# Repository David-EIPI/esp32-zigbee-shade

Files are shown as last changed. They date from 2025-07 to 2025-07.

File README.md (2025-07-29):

# esp32-zigbee-shade

## Overview

This external window shade is designed to shield the room from sunlight, reducing the load on the air conditioner. I upgraded a basic corded roller shade by integrating a small DC motor and a Zigbee controller compatible with my Home Assistant network.

## Firmware

The firmware is written in C and built using `idf.py`.
It exposes 2 endpoints with 3 clusters:

* **Window covering** (shade control)
* **OTA** (remote firmware upgrade)
* **Temperature measurement** (on-chip temperature sensor)

The temperature sensor reports via Zigbee to monitor the temperature inside the control box, as summer ambient temperatures often exceed 35°C, and the enclosure tightly houses both the ESP32 and the motor driver.

See [here](https://github.com/David-EIPI/esp32-zigbee-light/blob/main/BUILD.md) instructions on building the firmware using `idf.py` on Linux.

## Hardware

### Mechanical

This window cover is based on the VICLLAX 5×6 ft corded roll-up shade, which uses an aluminum tube with a 1 1/8" (28 mm) inner diameter.

Several inexpensive DC motors with pre-assembled gearheads are available online, commonly found as clones of the Bringsmart High Torque Worm Gear DC motor. Most of these motors use gearheads with D-shaped shafts, predominantly 8 mm but occasionally 6 mm.

These motors and gearboxes come in various voltages and torque ratings. I used a 12 V motor equipped with a 200× ratio gearbox rated for 4 kg·cm torque. This choice turned out to be excessive, as a gearbox with a 60× or 80× ratio would have been sufficient.

To couple the motor to the roller tube, I repurposed Zemismart’s replacement 28 mm nylon gears, removing one tooth from each side and filing the D-shaped channel to match the motor shaft.

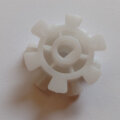
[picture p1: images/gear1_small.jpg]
OriginalGear The original gear

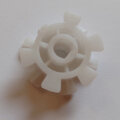
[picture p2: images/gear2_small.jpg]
ModifiedGear Modified gear
\
*The original gear compared to the modified gear (two teeth removed, D-shape filed).*

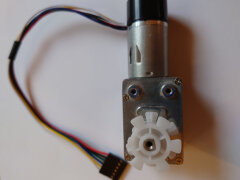
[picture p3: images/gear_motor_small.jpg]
GearMotor Gear fits the motor
\
*Gear mounted on the motor shaft.*

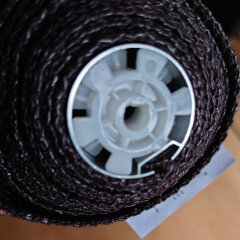
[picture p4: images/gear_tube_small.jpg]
GearTube Gear fits the tube
\
*Gear inserted into the shade tube.*

For motor mounting, I modified the original bracket supplied with the shade. I broke off the support lip, drilled two additional holes, and added a countersunk hole at the existing cut. The modified bracket is shown below:

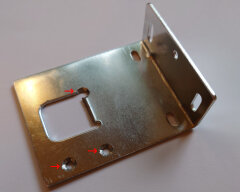
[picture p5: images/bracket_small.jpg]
Bracket


The image below shows the fully assembled motor with the coupling gear:

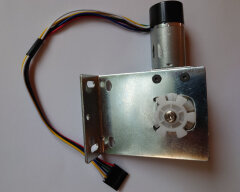
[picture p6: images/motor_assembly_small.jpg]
Assembly


### Electronics

The control system uses an ESP32-H2 chip on Tenstar’s Supermini board (or a clone). [This board sometimes exhibits startup issues](https://github.com/David-EIPI/esp32-zigbee-light) when powered from a standalone DC-DC converter. Although the board already has an RC circuit on its reset line, it is apparently insufficient, as intermittent boot failures occur on power-up. I resolved this issue by soldering an additional 0.22 µF capacitor in parallel with the existing one.

The ESP32-H2 Supermini clones available on Aliexpress vary. The most notable difference is component placement: some boards have all components mounted on the top side, while other (usually cheaper) versions have components on both sides. For the double-sided boards, the additional capacitor should be soldered on the bottom side, as shown in the photo. Although I only had 0603-sized capacitors at hand, it fit comfortably next to the existing one.

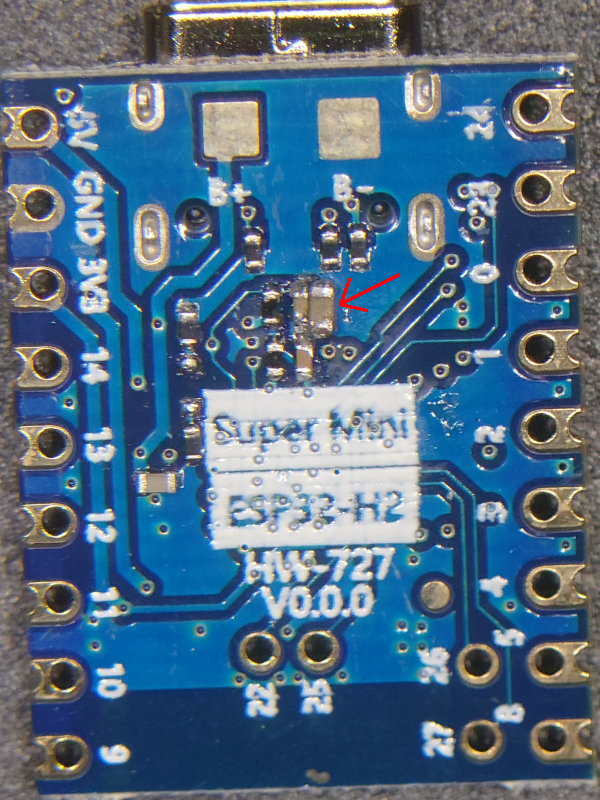
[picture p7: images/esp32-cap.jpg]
Bottom side cap Capacitor


Due to bottom-side components, the ESP32-H2 board must be mounted above the mainboard:

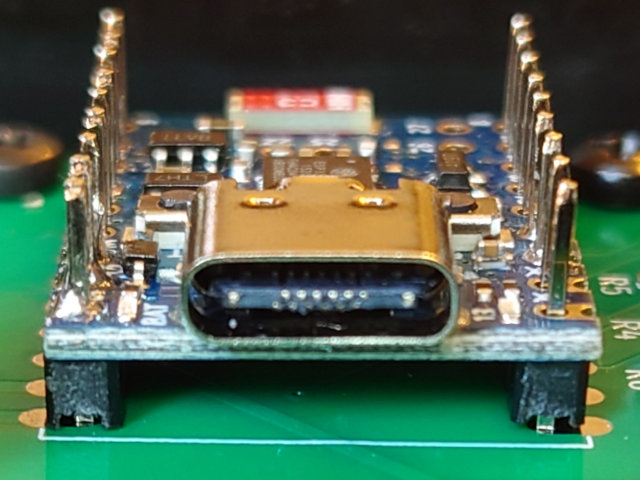
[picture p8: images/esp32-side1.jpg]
Elevated board Elevated


The motor driver uses a DRV8871 chip from Texas Instruments. It accepts a PWM control signal, easily generated using the standard ESP32 `ledc` controller.

The motor features a rotary encoder interfaced to the ESP32’s standard pulse-counter controller. This encoder maintains consistent upper and lower travel limits and allows precise partially-open positioning of the shade.

A notable drawback of this motor is its hardwired, non-weatherproof cable. Its durability in summer humidity remains uncertain, and some corrosion is likely inevitable. To minimize electrochemical corrosion, I designed the control circuit to disconnect power from the motor and encoder when the shade is stationary.

The final assembly fits neatly into the Serpac 110i BK enclosure. I only needed to cut openings for the 6-pin motor connector (on the left) and the power jack (on the right):

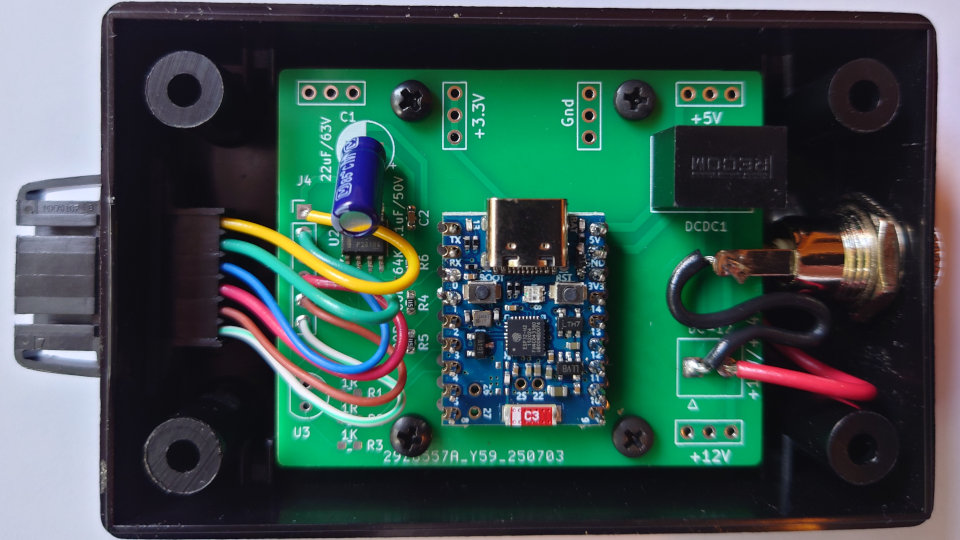
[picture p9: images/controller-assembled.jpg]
Controller assembly Controller


Since the motor connector is not polarized it may be a good idea to mark the connector orientation on the enclosure side.

## ZHA quirk

Although ZHA supports window coverings, additional configuration using a quirk is required. The quirk provides coverage percentage display, lift velocity settings, and essential calibration buttons for setting upper and lower limits.

The screenshot below shows the device page (quirk applied):

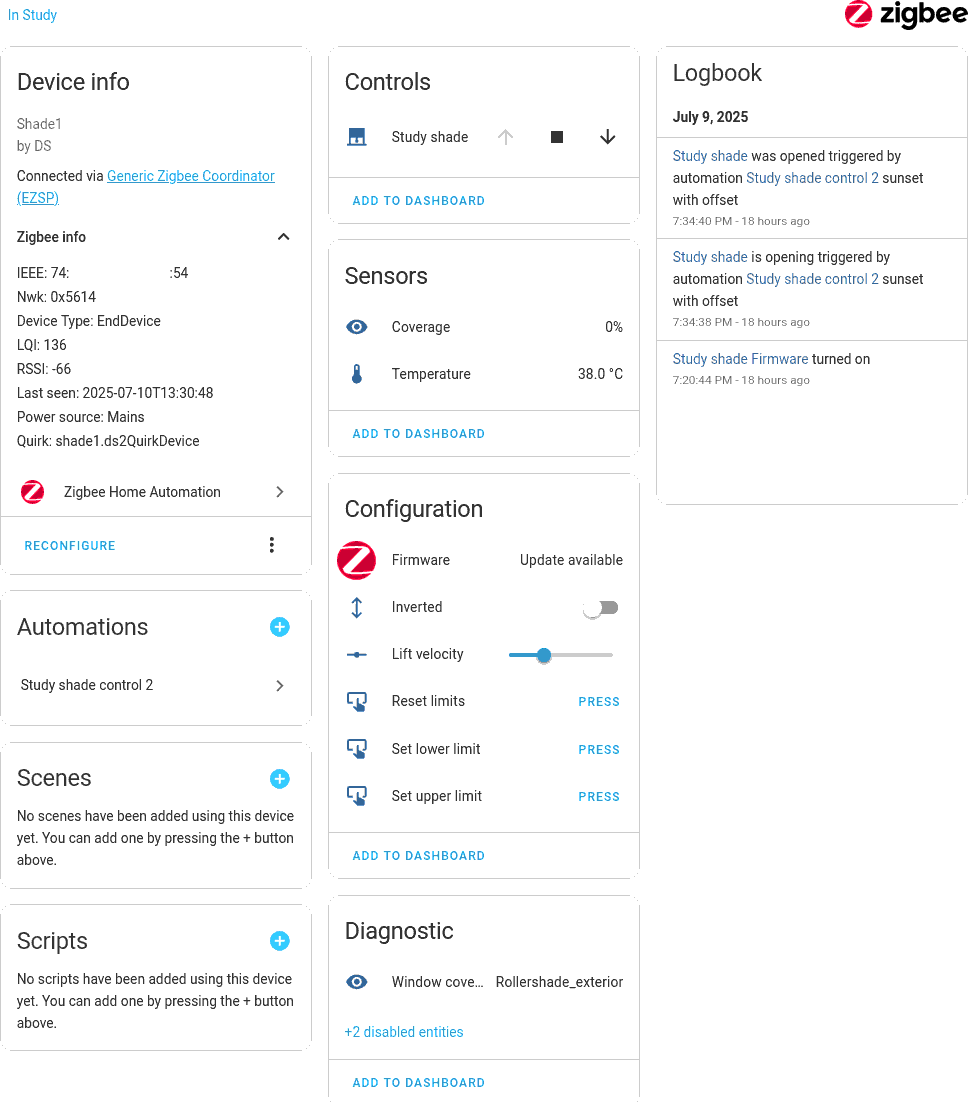
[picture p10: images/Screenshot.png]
Device info


Calibration of limits must be completed before using the shade for the first time. The calibration procedure is as follows:

* Press "↓" to start lowering the shade, stopping roughly halfway.
  This step isn't strictly required, but it reduces the likelihood of pulse counter overflow, as the pulse counter range is limited to 16 bits.
* Press "reset limits".
* Press "↑" to raise the shade, stopping at the desired upper position. Then press "Set upper limit" to record this position.
* Press "↓" again, stopping at the desired lower position. Then press "Set lower limit" to record this position.

Depending on Zigbee network topology, commands may take about a second to process. Thus, if the motor rolls quickly, reducing the lift velocity before calibration may improve accuracy.

## Over-the-air (OTA) upgrade

The firmware supports OTA upgrades. ESP's Zigbee library handles most tasks, leaving only four essential `esp_ota_*` function calls (`begin`, `data`, `write`, and `end`) for firmware implementation, aside from cluster allocation and error checking. The SDK provides an image builder tool (`image_builder_tool.py`) to convert compiled firmware into OTA format (see the `ota_image.sh` script for a usage example).

On the Home Assistant side, the Zigpy configuration should be added to `configuration.yaml` under the `zha:` section, as illustrated below:

```
zha:
  zigpy_config:
    ota:
      extra_providers:
        - type: zigpy_local
          index_file: /config/zha_ota/local_index.json
        - type: advanced
          warning: I understand I can *destroy* my devices by enabling OTA
              updates from files. Some OTA updates can be mistakenly applied to the
              wrong device, breaking it. I am consciously using this at my own risk.
          path: /config/zha_ota
```

OTA update files (JSON and BIN) should be uploaded to the specified directory (`/config/zha_ota` in this example). When using the JSON OTA provider, Home Assistant will display firmware version and release notes from the provided JSON file.

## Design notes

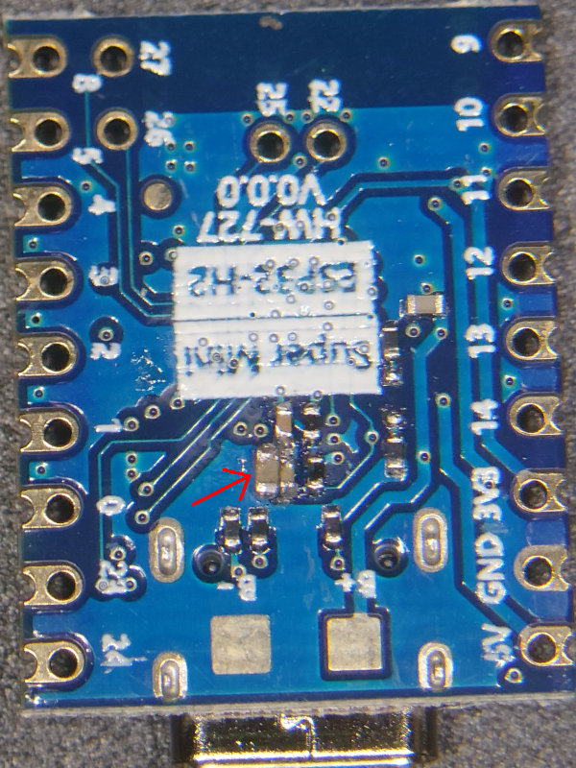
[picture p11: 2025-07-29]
images/esp32-cap1.jpg

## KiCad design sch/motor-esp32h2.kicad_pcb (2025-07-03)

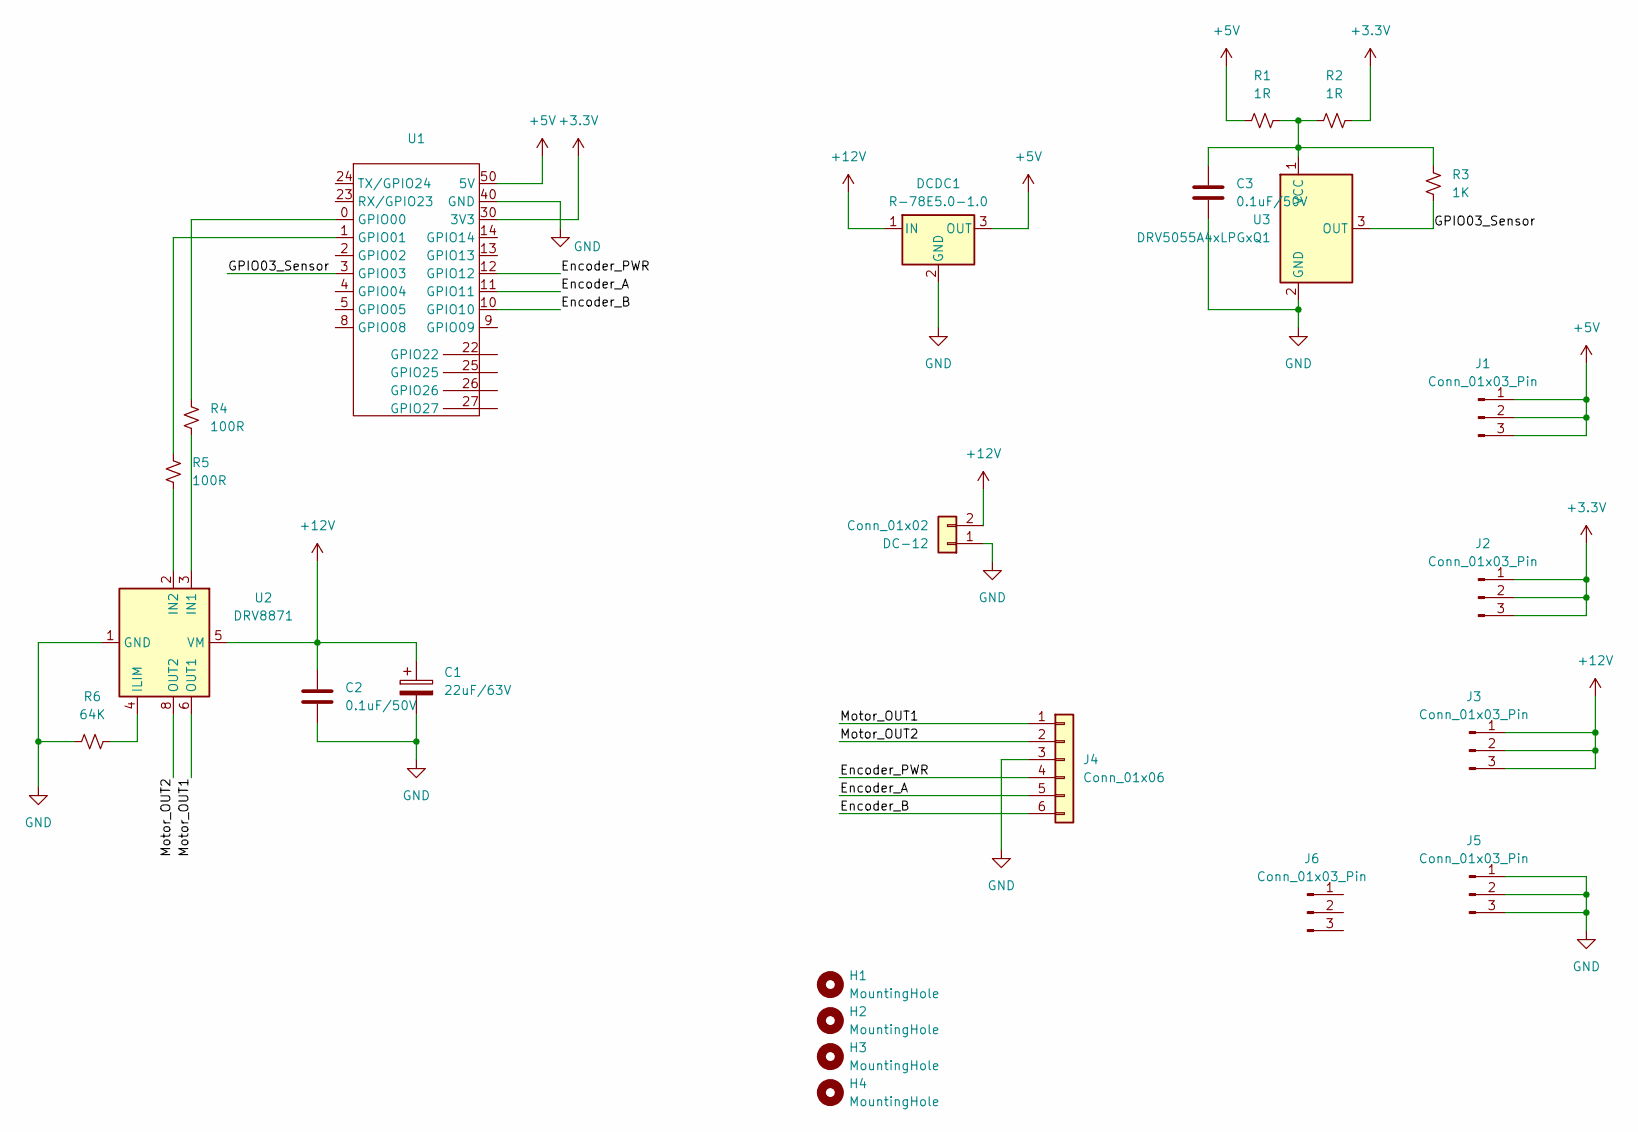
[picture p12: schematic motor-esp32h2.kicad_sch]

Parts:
C1: 22uF/63V; CP_Radial_D6.3mm_P2.50mm
C2, C3: 0.1uF/50V; C_0603_1608Metric_Pad1.08x0.95mm_HandSolder
DC-12: Conn_01x02; TE_826576-2_1x02_P3.96mm_Vertical
DCDC1: R-78E5.0-1.0; Converter_DCDC_RECOM_R-78E-0.5_THT
H1, H2, H3, H4: MountingHole; MountingHole_2.7mm_M2.5
J1, J2, J3, J5, J6: Conn_01x03_Pin; PinHeader_1x03_P2.54mm_Vertical
J4: Conn_01x06; PinHeader_1x06_P2.54mm_Vertical
R1, R2: 1R; R_0603_1608Metric_Pad0.98x0.95mm_HandSolder
R3: 1K; R_0603_1608Metric_Pad0.98x0.95mm_HandSolder
R4, R5: 100R; R_0603_1608Metric_Pad0.98x0.95mm_HandSolder
R6: 64K; R_0603_1608Metric_Pad0.98x0.95mm_HandSolder
U1: ESP32-H2-SuperMini
U2: DRV8871; Texas_HTSOP-8-1EP_3.9x4.9mm_P1.27mm_EP2.95x4.9mm_Mask2.4x3.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
U3: DRV5055A4xLPGxQ1; TO-92_Inline

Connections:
+3.3V: J2.1, J2.2, J2.3, R2.2, U1.30 (3V3)
+5V: DCDC1.3 (OUT), J1.1, J1.2, J1.3, R1.1, U1.50 (5V)
+12V: C1.1, C2.1, DC-12.2, DCDC1.1 (IN), J3.1, J3.2, J3.3, U2.5 (VM)
/Encoder_A: J4.5, U1.11 (GPIO11)
/Encoder_B: J4.6, U1.10 (GPIO10)
/Encoder_PWR: J4.4, U1.12 (GPIO12)
/GPIO03_Sensor: R3.1, U1.3 (GPIO03), U3.3 (OUT)
/Motor_OUT1: J4.1, U2.6 (OUT1)
/Motor_OUT2: J4.2, U2.8 (OUT2)
GND: C1.2, C2.2, C3.2, DC-12.1, DCDC1.2 (GND), J4.3, J5.1, J5.2, J5.3, R6.1, U1.40 (GND), U2.1 (GND), U2.7 (GND), U2.9 (GND), U3.2 (GND)
unnamed: R4.1, U1.0 (GPIO00)
unnamed: R5.1, U1.1 (GPIO01)
unnamed: R6.2, U2.4 (ILIM)
unnamed: R4.2, U2.3 (IN1)
unnamed: R5.2, U2.2 (IN2)
unnamed: C3.1, R1.2, R2.1, R3.2, U3.1 (VCC)

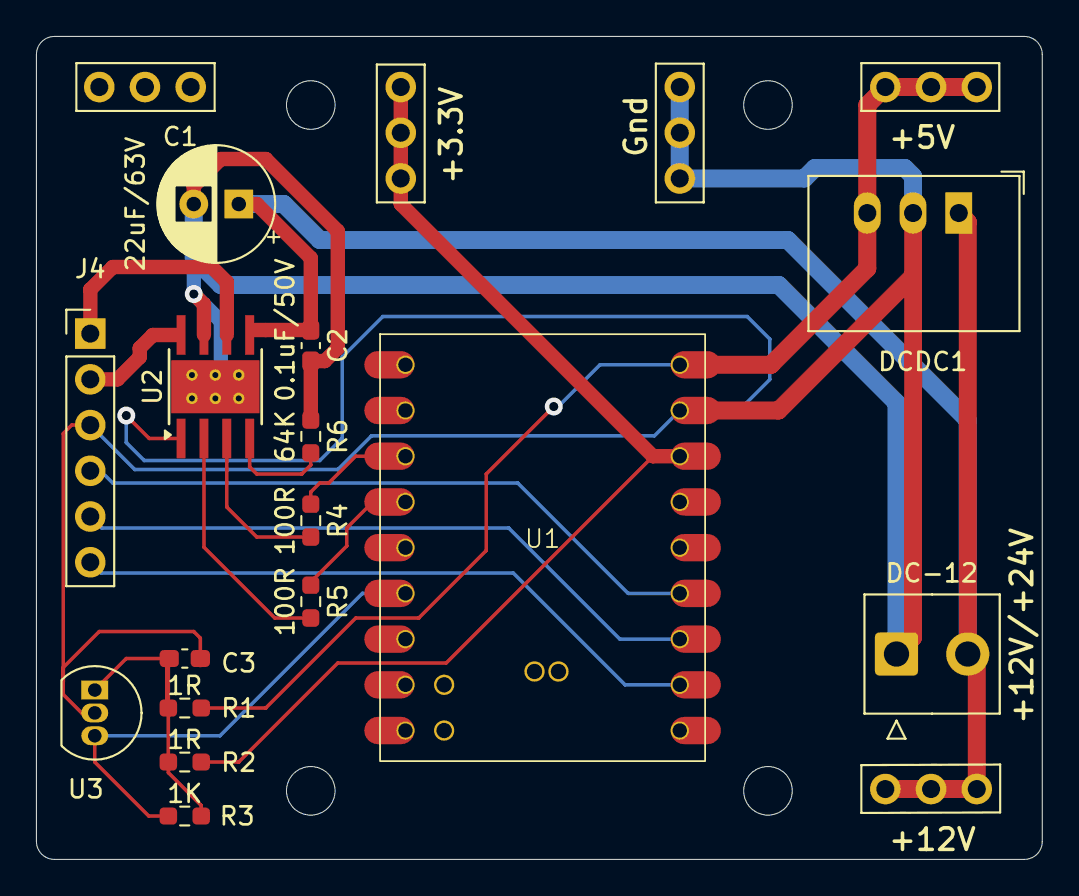
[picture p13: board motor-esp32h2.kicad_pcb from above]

Board: 2 copper layers, 55.9 x 45.7 mm, 24 parts (0 on the bottom side), 16 nets.

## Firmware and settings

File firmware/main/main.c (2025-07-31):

/*
 * Zigbee Roller Shade Example
 *
 * Unless required by applicable law or agreed to in writing, this
 * software is distributed on an "AS IS" BASIS, WITHOUT WARRANTIES OR
 * CONDITIONS OF ANY KIND, either express or implied.
 * 2025/07
 * License: BSD-2
 */

#include <string.h>
#include "freertos/FreeRTOS.h"
#include "freertos/task.h"
#include "esp_check.h"
#include "esp_zigbee_core.h"
#include "esp_log.h"
#include "nvs_flash.h"
#include "ha/esp_zigbee_ha_standard.h"
#include "driver/gpio.h"
#include "driver/temperature_sensor.h"
#include "main.h"
#include "clock.h"
#include "encoder.h"
#include "motor.h"
#include "ota.h"


#if !defined ZB_ED_ROLE
#error Define ZB_ED_ROLE in idf.py menuconfig to compile light (End Device) source code.
#endif


enum _queue_message_code {
    QM_UNKNOWN = 0,
    QM_FROM_ENCODER,
    QM_ZIGBEE_STOP,
    QM_ZIGBEE_UP,
    QM_ZIGBEE_DOWN,
    QM_ZIGBEE_TO_VALUE,
    QM_ZIGBEE_TO_PERCENTAGE,
    QM_ZIGBEE_SET_UPPER,
    QM_ZIGBEE_SET_LOWER,
    QM_ZIGBEE_RESET_LIMITS,
    QM_ZIGBEE_SET_VELOCITY,
    QM_ZIGBEE_SET_MODE,
};


static const char *ZB_TAG = "APP_ZIGBEE";
static const char *MAIN_TAG = "APP_MAIN";

static const unsigned indication_led_pin = 13;

static const uint32_t timer_resolution = 10 * 1000;
static gptimer_handle_t timer = 0;

TaskHandle_t motorTaskHandle = NULL;

static temperature_sensor_handle_t temp_handle = NULL;
static float temperature_sensor_value = 0;


/* The queue is to be created to hold a maximum of 16 uint32_t  variables. */
#define QUEUE_LENGTH      16
#define QUEUE_ITEM_SIZE   sizeof( uint32_t )

/* The variable used to hold the queue's data structure. */
static StaticQueue_t xStaticQueue;

/* The array to use as the queue's storage area. This must be at least uxQueueLength * uxItemSize bytes. */
static uint8_t ucQueueStorageArea[ QUEUE_LENGTH * QUEUE_ITEM_SIZE ];

/* Main task queue is used to send commands and data to the main task */
QueueHandle_t xMainQueue;

/* Position monitoring. current_pos = last reading from the encoder */
static int32_t currentPosition = 0;
/* Position monitoring. previous_pos = previous reading */
static int previousPosition = 0;
/* Position monitoring. target_pos = requested position.
The motor must spin towards target_pos, otherwise we should stop it. */
static int targetPosition = 0;

/*
    Save position to NVS when it changes by this amount.
    Position is also saved every time the motor stops.
 */
static const int32_t movingSaveDelta = ENCODER_PULSE_PER_REV;
/*
    NVS saving delta when motor is stationary accounts for backlash.
*/
static const int32_t staticSaveDelta = 20;

/* Approximate lift velocity at max motor speed, cm/s */
static const int maxLiftVelocity = 10;

/* Lift velocity requested via Zigbee */
static int32_t zbLiftVelocity = 5;

/* Upper and lower lift limits. Must be calibrated via Zigbee */
static int32_t upperLiftLimit = ENCODER_MAX_LIMIT;
static int32_t lowerLiftLimit = ENCODER_MIN_LIMIT;

/* Fixed upper and lower limits reported to clients */
static int32_t zb_UpperLiftLimit = 180;
static int32_t zb_LowerLiftLimit = 0;

/* User configured coverage limit, % */
static int32_t zb_userPercentageLimit = 100;

/* Inversion flag. Changes percentage assigment and up/down buttons' directions. */
static int zb_Inversion = 0;

/* NVS keys */
const char ZB_STORAGE_NAMESPACE[] = "zb_storage";

static char nvs_UpperLimit[] = "W_UL";
static char nvs_LowerLimit[] = "W_LL";
static char nvs_zbUpperLimit[] = "WZUL";
static char nvs_zbLowerLimit[] = "WZLL";
static char nvs_Velocity[] = "W_Ve";
static char nvs_ModeAttr[] = "W_MA";
static char nvs_CurrentPosition[] = "W_CP";

/********************* Utility functions **************************/

static int encoder_to_zigbee(int position, int zb_min, int zb_max)
{
    if (zb_min == zb_max ||
        upperLiftLimit == lowerLiftLimit) {
        return 0;
    }

    int encmin = lowerLiftLimit;
    int diff = upperLiftLimit - lowerLiftLimit;

/* Allow inversion */
    if (diff < 0) {
        diff = -diff;
        encmin = upperLiftLimit;
    }

    int zb_pos = zb_min + ((position - encmin) * (zb_max - zb_min)) / diff;
    if (zb_pos < zb_min) zb_pos = zb_min;
    else if (zb_pos > zb_max) zb_pos = zb_max;
    return zb_pos;
}

static int encoder_to_zigbee_units(int position)
{
    return encoder_to_zigbee(position, zb_LowerLiftLimit, zb_UpperLiftLimit);
}

static int encoder_to_zigbee_percentage(int position)
{
    uint8_t p = encoder_to_zigbee(position, 0, 100);
    if (!zb_Inversion)
        p = 100 - p;

    return p;
}

static int zigbee_to_encoder(int zb_position, int zb_min, int zb_max)
{
    if (zb_min == zb_max ||
        upperLiftLimit == lowerLiftLimit) {
        return 0;
    }

    int encmin = lowerLiftLimit;
    int diff = upperLiftLimit - lowerLiftLimit;

/* Allow inversion */
    if (diff < 0) {
        diff = -diff;
        encmin = upperLiftLimit;
    }

    int pos = encmin + ((zb_position - zb_min) * diff) / (zb_max - zb_min);
    if (pos > upperLiftLimit) pos = upperLiftLimit;
    else if (pos < lowerLiftLimit) pos = lowerLiftLimit;

    return pos;
}

static int zigbee_units_to_encoder(int zb_position)
{
    return zigbee_to_encoder(zb_position, zb_LowerLiftLimit, zb_UpperLiftLimit);
}

static int zigbee_percentage_to_encoder(int zb_position)
{
    int p = zb_position;
    if (p < 0) p = 0;
    if (p > 100) p = 100;
    if (!zb_Inversion)
        p = 100 - p;

    return zigbee_to_encoder(p, 0, 100);
}


/********************* Zigbee functions **************************/
static void bdb_start_top_level_commissioning_cb(uint8_t mode_mask)
{
    ESP_ERROR_CHECK(esp_zb_bdb_start_top_level_commissioning(mode_mask));
}

static const int ZB_INIT_FAIL_COUNT_TO_REBOOT = 60;
static const int ZB_ZDO_FAIL_COUNT_TO_REBOOT = 10;
static int zb_fail_count = 0;

static void init_gpio(void)
{
    const gpio_config_t io_conf = {
        .intr_type = GPIO_INTR_DISABLE,
        .mode = GPIO_MODE_OUTPUT,
        .pin_bit_mask = (1ULL << indication_led_pin),
        .pull_down_en = 0,
        .pull_up_en = 0,
    };

    gpio_config(&io_conf);
    gpio_set_level(indication_led_pin, 1);
}


void esp_zb_app_signal_handler(esp_zb_app_signal_t *signal_struct)
{
    uint32_t *p_sg_p       = signal_struct->p_app_signal;
    esp_err_t err_status = signal_struct->esp_err_status;
    esp_zb_app_signal_type_t sig_type = *p_sg_p;
    uint8_t min_lqi;

    switch (sig_type) {
    case ESP_ZB_NLME_STATUS_INDICATION:
        ESP_LOGI(ZB_TAG, "%s, status: 0x%x\n", esp_zb_zdo_signal_to_string(sig_type), *(uint8_t *)esp_zb_app_signal_get_params(p_sg_p));
        break;
    case ESP_ZB_ZDO_SIGNAL_SKIP_STARTUP:
        ESP_LOGI(ZB_TAG, "Zigbee stack initialized");
        esp_zb_bdb_start_top_level_commissioning(ESP_ZB_BDB_MODE_INITIALIZATION);
        min_lqi = esp_zb_secur_network_min_join_lqi_get();
        ESP_LOGI(ZB_TAG, "Min LQI = %u", (unsigned)min_lqi);
        esp_zb_secur_network_min_join_lqi_set(0);
        break;
    case ESP_ZB_BDB_SIGNAL_DEVICE_FIRST_START:
    case ESP_ZB_BDB_SIGNAL_DEVICE_REBOOT:
        if (err_status == ESP_OK) {
            ESP_LOGI(ZB_TAG, "Device started up in %s factory-reset mode", esp_zb_bdb_is_factory_new() ? "" : "non");
            if (esp_zb_bdb_is_factory_new()) {
                ESP_LOGI(ZB_TAG, "Start network steering");
                esp_zb_bdb_start_top_level_commissioning(ESP_ZB_BDB_MODE_NETWORK_STEERING);
            } else {
                ESP_LOGI(ZB_TAG, "Device rebooted");
            }

            zb_fail_count = 0;
        } else {
            /* commissioning failed */

            if (ZB_INIT_FAIL_COUNT_TO_REBOOT <= zb_fail_count) {
                ESP_LOGI(ZB_TAG, "ZB init has failed too many times. Restarting.");
                break;
            }

            ESP_LOGW(ZB_TAG, "Failed to initialize Zigbee stack (status: %s)", esp_err_to_name(err_status));
            esp_zb_scheduler_alarm((esp_zb_callback_t)bdb_start_top_level_commissioning_cb, ESP_ZB_BDB_MODE_INITIALIZATION, 1000);
            zb_fail_count += 1;
        }
        break;
    case ESP_ZB_BDB_SIGNAL_STEERING:
        if (err_status == ESP_OK) {
            esp_zb_ieee_addr_t extended_pan_id;
            esp_zb_get_extended_pan_id(extended_pan_id);
            ESP_LOGI(ZB_TAG, "Joined network successfully (Extended PAN ID: %02x:%02x:%02x:%02x:%02x:%02x:%02x:%02x, PAN ID: 0x%04hx, Channel:%d, Short Address: 0x%04hx)",
                     extended_pan_id[7], extended_pan_id[6], extended_pan_id[5], extended_pan_id[4],
                     extended_pan_id[3], extended_pan_id[2], extended_pan_id[1], extended_pan_id[0],
                     esp_zb_get_pan_id(), esp_zb_get_current_channel(), esp_zb_get_short_address());
        } else {
            ESP_LOGI(ZB_TAG, "Network steering was not successful (status: %s)", esp_err_to_name(err_status));
            esp_zb_scheduler_alarm((esp_zb_callback_t)bdb_start_top_level_commissioning_cb, ESP_ZB_BDB_MODE_NETWORK_STEERING, 1000);
        }
        break;
    case ESP_ZB_ZDO_SIGNAL_LEAVE:
        ESP_LOGI(ZB_TAG, "Leave and network steering initiated.");
        esp_zb_factory_reset();
        esp_zb_scheduler_alarm((esp_zb_callback_t)bdb_start_top_level_commissioning_cb, ESP_ZB_BDB_MODE_NETWORK_STEERING, 1000);
        break;
    case ESP_ZB_ZDO_DEVICE_UNAVAILABLE:
        if (ZB_ZDO_FAIL_COUNT_TO_REBOOT <= zb_fail_count) {
            ESP_LOGI(ZB_TAG, "ZDO device unavailable. Restarting.");
            esp_restart();
            break;
        }
        zb_fail_count += 1;
        __attribute__ ((fallthrough));
    default:
        ESP_LOGI(ZB_TAG, "ZDO signal: %s (0x%x), status: %s", esp_zb_zdo_signal_to_string(sig_type), sig_type,
                 esp_err_to_name(err_status));
        break;
    }
}


/* Setup window covering cluster */
static struct _zb_WindowCoveringAttrs {
    uint8_t windowCoveringType;
    uint16_t currentPosition;
    uint8_t configStatus;
    uint8_t currentPercentage;
    int32_t mode;
} zb_WindowCoveringAttrs = {
    .windowCoveringType = ESP_ZB_ZCL_ATTR_WINDOW_COVERING_TYPE_ROLLERSHADE_EXTERIOR,
    .currentPosition = 0, //cm
    .configStatus = ESP_ZB_ZCL_ATTR_WINDOW_COVERING_CONFIG_OPERATIONAL     |
        ESP_ZB_ZCL_ATTR_WINDOW_COVERING_CONFIG_ONLINE                      |
        ESP_ZB_ZCL_ATTR_WINDOW_COVERING_CONFIG_LIFT_CONTROL_IS_CLOSED_LOOP |
        ESP_ZB_ZCL_ATTR_WINDOW_COVERING_CONFIG_LIFT_ENCODER_CONTROLLED,
    .currentPercentage = 0,
/*
    ESP32 Zigbee SDK has a bug that considers mode=0 (no flags set) an invalid value.
    Therefore, we assign an unused but harmless flag here to make SDK functions happy and accept this attribute.
*/
    .mode = ESP_ZB_ZCL_ATTR_WINDOW_COVERING_TYPE_LEDS_WILL_DISPLAY_FEEDBACK,
};

static struct {
    int id;
    void *value_ptr;
    int type;
    int access;
} window_covering_attr_desc[] = {
    { ESP_ZB_ZCL_ATTR_WINDOW_COVERING_WINDOW_COVERING_TYPE_ID      ,       &zb_WindowCoveringAttrs.windowCoveringType, .type = ESP_ZB_ZCL_ATTR_TYPE_8BIT_ENUM, .access = ESP_ZB_ZCL_ATTR_ACCESS_READ_ONLY},
    { ESP_ZB_ZCL_ATTR_WINDOW_COVERING_PHYSICAL_CLOSED_LIMIT_LIFT_ID,       &zb_UpperLiftLimit,                         .type = ESP_ZB_ZCL_ATTR_TYPE_U16,       .access = ESP_ZB_ZCL_ATTR_ACCESS_READ_ONLY},
    { ESP_ZB_ZCL_ATTR_WINDOW_COVERING_CURRENT_POSITION_LIFT_ID,            &zb_WindowCoveringAttrs.currentPosition,    .type = ESP_ZB_ZCL_ATTR_TYPE_U16,       .access = ESP_ZB_ZCL_ATTR_ACCESS_READ_ONLY | ESP_ZB_ZCL_ATTR_ACCESS_REPORTING },
    { ESP_ZB_ZCL_ATTR_WINDOW_COVERING_CONFIG_STATUS_ID,                    &zb_WindowCoveringAttrs.configStatus,       .type = ESP_ZB_ZCL_ATTR_TYPE_8BITMAP,   .access = ESP_ZB_ZCL_ATTR_ACCESS_READ_ONLY },
    { ESP_ZB_ZCL_ATTR_WINDOW_COVERING_CURRENT_POSITION_LIFT_PERCENTAGE_ID, &zb_WindowCoveringAttrs.currentPercentage,  .type = ESP_ZB_ZCL_ATTR_TYPE_U8,        .access = ESP_ZB_ZCL_ATTR_ACCESS_READ_ONLY | ESP_ZB_ZCL_ATTR_ACCESS_REPORTING | ESP_ZB_ZCL_ATTR_ACCESS_SCENE },
    { ESP_ZB_ZCL_ATTR_WINDOW_COVERING_INSTALLED_OPEN_LIMIT_LIFT_ID,        &zb_UpperLiftLimit,                         .type = ESP_ZB_ZCL_ATTR_TYPE_U16,       .access = ESP_ZB_ZCL_ATTR_ACCESS_READ_WRITE },
    { ESP_ZB_ZCL_ATTR_WINDOW_COVERING_INSTALLED_CLOSED_LIMIT_LIFT_ID,      &zb_LowerLiftLimit,                         .type = ESP_ZB_ZCL_ATTR_TYPE_U16,       .access = ESP_ZB_ZCL_ATTR_ACCESS_READ_WRITE },
    { ESP_ZB_ZCL_ATTR_WINDOW_COVERING_VELOCITY_ID,                         &zbLiftVelocity,                            .type = ESP_ZB_ZCL_ATTR_TYPE_U16,       .access = ESP_ZB_ZCL_ATTR_ACCESS_READ_WRITE },
    { ESP_ZB_ZCL_ATTR_WINDOW_COVERING_MODE_ID,                             &zb_WindowCoveringAttrs.mode,               .type = ESP_ZB_ZCL_ATTR_TYPE_8BITMAP,   .access = ESP_ZB_ZCL_ATTR_ACCESS_READ_WRITE },
};

static esp_zb_attribute_list_t * create_window_covering_cluster(void)
{
    zb_Inversion = 0 != (zb_WindowCoveringAttrs.mode & ESP_ZB_ZCL_ATTR_WINDOW_COVERING_TYPE_REVERSED_MOTOR_DIRECTION);

    if (zb_Inversion) {
        zb_WindowCoveringAttrs.configStatus |= ESP_ZB_ZCL_ATTR_WINDOW_COVERING_CONFIG_REVERSE_COMMANDS;
    } else {
        zb_WindowCoveringAttrs.configStatus &= ~ESP_ZB_ZCL_ATTR_WINDOW_COVERING_CONFIG_REVERSE_COMMANDS;
    }

    esp_zb_attribute_list_t * window_covering_cluster =
        esp_zb_zcl_attr_list_create(ESP_ZB_ZCL_CLUSTER_ID_WINDOW_COVERING);


    if (window_covering_cluster) {
        unsigned i;
        for (i = 0; i < lengthof(window_covering_attr_desc); i++) {
                ESP_ERROR_CHECK_WITHOUT_ABORT(
                        ((window_covering_attr_desc[i].id == ESP_ZB_ZCL_ATTR_WINDOW_COVERING_INSTALLED_OPEN_LIMIT_LIFT_ID) ||
                         (window_covering_attr_desc[i].id == ESP_ZB_ZCL_ATTR_WINDOW_COVERING_INSTALLED_CLOSED_LIMIT_LIFT_ID)) ?
                    esp_zb_cluster_add_attr(
                        window_covering_cluster,
                        ESP_ZB_ZCL_CLUSTER_ID_WINDOW_COVERING,
                        window_covering_attr_desc[i].id,
                        window_covering_attr_desc[i].type,
                        window_covering_attr_desc[i].access,
                        window_covering_attr_desc[i].value_ptr
                    )
                    :
                    esp_zb_window_covering_cluster_add_attr(
                        window_covering_cluster,
                        window_covering_attr_desc[i].id,
                        window_covering_attr_desc[i].value_ptr
                    )
                );
        }
    }
    return window_covering_cluster;
}


/* Setup Temperature Sensor cluster */
static esp_zb_attribute_list_t * create_temperature_cluster(void)
{
    esp_zb_temperature_meas_cluster_cfg_t cfg = { 0, -10 * 100, 80 * 100 };
    esp_zb_attribute_list_t * temperature_measurement_cluster = esp_zb_temperature_meas_cluster_create(&cfg);

    return temperature_measurement_cluster;
}

/* Analog output clusters - to support user settings */

static struct {
    char     description[16];
    float    min_present;
    float    max_present;
    float    present_value;
    float    resolution;
    uint16_t status_flags;
    uint16_t units;
    uint32_t app_type;
    volatile int32_t *value_ptr;
} analog_output_attr_values[] = {
    {
    .description = "\x0e" "Coverage limit",
    .min_present = 0,
    .max_present = 100,
    .present_value = 100,
    .resolution = 1,
    .status_flags = 0,
    .units = 98, /* 98 = % */
    .app_type = 16 << 16, /* 16 = brightness-percent */
    .value_ptr = &zb_userPercentageLimit,
    },
};

#define ANALOG_ATTR_FIELD_OFFSET(field) (offsetof(typeof(analog_output_attr_values[0]), field))

static struct {
    int id;
    int offs;
    int access;
} analog_attr_offset[] = {
    { ESP_ZB_ZCL_ATTR_ANALOG_OUTPUT_DESCRIPTION_ID      , ANALOG_ATTR_FIELD_OFFSET(description),   .access = ESP_ZB_ZCL_ATTR_ACCESS_READ_ONLY },
    { ESP_ZB_ZCL_ATTR_ANALOG_OUTPUT_MAX_PRESENT_VALUE_ID, ANALOG_ATTR_FIELD_OFFSET(max_present),   .access = ESP_ZB_ZCL_ATTR_ACCESS_READ_ONLY },
    { ESP_ZB_ZCL_ATTR_ANALOG_OUTPUT_MIN_PRESENT_VALUE_ID, ANALOG_ATTR_FIELD_OFFSET(min_present),   .access = ESP_ZB_ZCL_ATTR_ACCESS_READ_ONLY },
    { ESP_ZB_ZCL_ATTR_ANALOG_OUTPUT_PRESENT_VALUE_ID    , ANALOG_ATTR_FIELD_OFFSET(present_value), .access = ESP_ZB_ZCL_ATTR_ACCESS_READ_WRITE | ESP_ZB_ZCL_ATTR_ACCESS_REPORTING },
    { ESP_ZB_ZCL_ATTR_ANALOG_OUTPUT_RESOLUTION_ID       , ANALOG_ATTR_FIELD_OFFSET(resolution),    .access = ESP_ZB_ZCL_ATTR_ACCESS_READ_ONLY },
    { ESP_ZB_ZCL_ATTR_ANALOG_OUTPUT_STATUS_FLAGS_ID     , ANALOG_ATTR_FIELD_OFFSET(status_flags),  .access = ESP_ZB_ZCL_ATTR_ACCESS_READ_WRITE },
    { ESP_ZB_ZCL_ATTR_ANALOG_OUTPUT_ENGINEERING_UNITS_ID, ANALOG_ATTR_FIELD_OFFSET(units),         .access = ESP_ZB_ZCL_ATTR_ACCESS_READ_ONLY },
    { ESP_ZB_ZCL_ATTR_ANALOG_OUTPUT_APPLICATION_TYPE_ID , ANALOG_ATTR_FIELD_OFFSET(app_type),      .access = ESP_ZB_ZCL_ATTR_ACCESS_READ_ONLY }
};

static esp_zb_attribute_list_t * create_analog_cluster(unsigned cl_idx)
{
    esp_zb_attribute_list_t *esp_zb_analog_cluster = esp_zb_zcl_attr_list_create(ESP_ZB_ZCL_CLUSTER_ID_ANALOG_OUTPUT);
    int nattrs = 0;
    if (esp_zb_analog_cluster != NULL) {

        analog_output_attr_values[cl_idx].present_value = *analog_output_attr_values[cl_idx].value_ptr;

        int i;
        for (i = 0; i < lengthof(analog_attr_offset); i++) {
	    esp_err_t err = esp_zb_analog_output_cluster_add_attr(esp_zb_analog_cluster, analog_attr_offset[i].id,
	        ((void*)&analog_output_attr_values[cl_idx]) + analog_attr_offset[i].offs );
	    if (ESP_OK == err)
	        nattrs += 1;
        }
    }

    ESP_LOGI(ZB_TAG, "Analog output cluster %u created. Attrs: %d", cl_idx, nattrs);
    return esp_zb_analog_cluster;
}

/* Setup Basic cluster */
static esp_zb_attribute_list_t * create_basic_cluster(char *manufacturer)
{
    uint8_t zero = 0;
    uint8_t version = 3;

    esp_zb_attribute_list_t *esp_zb_basic_cluster = esp_zb_zcl_attr_list_create(ESP_ZB_ZCL_CLUSTER_ID_BASIC);

    if (esp_zb_basic_cluster != NULL) {
        esp_zb_basic_cluster_add_attr(esp_zb_basic_cluster, ESP_ZB_ZCL_ATTR_BASIC_MANUFACTURER_NAME_ID, manufacturer);
        esp_zb_basic_cluster_add_attr(esp_zb_basic_cluster, ESP_ZB_ZCL_ATTR_BASIC_MODEL_IDENTIFIER_ID, MODEL_IDENTIFIER);
        esp_zb_basic_cluster_add_attr(esp_zb_basic_cluster, ESP_ZB_ZCL_ATTR_BASIC_ZCL_VERSION_ID, &version);
        esp_zb_basic_cluster_add_attr(esp_zb_basic_cluster, ESP_ZB_ZCL_ATTR_BASIC_POWER_SOURCE_ID, &zero);
    }
    return esp_zb_basic_cluster;
}

esp_zb_zcl_reporting_info_t server_side_reporting_info[] = {

/* Window covering current position */
    {
        .direction = ESP_ZB_ZCL_CMD_DIRECTION_TO_SRV,
        .ep = HA_CLOSURE_ENDPOINT,
        .cluster_id = ESP_ZB_ZCL_CLUSTER_ID_WINDOW_COVERING,
        .cluster_role = ESP_ZB_ZCL_CLUSTER_SERVER_ROLE,
        .dst.profile_id = ESP_ZB_AF_HA_PROFILE_ID,
        .u.send_info.min_interval = 5, // Minimum interval of 5 seconds
        .u.send_info.max_interval = 600, // Maximum interval of 10 minutes
        .u.send_info.def_min_interval = 5, // Default minimum interval of 30 seconds
        .u.send_info.def_max_interval = 600, // Default maximum interval of 10 minutes
        .u.send_info.delta.u16 = 1, // Report on every state change
        .attr_id = ESP_ZB_ZCL_ATTR_WINDOW_COVERING_CURRENT_POSITION_LIFT_PERCENTAGE_ID,
        .manuf_code = ESP_ZB_ZCL_ATTR_NON_MANUFACTURER_SPECIFIC, //0xFFFF,
    },


};

static void setup_reporting(void)
{

    unsigned idx;
/* Config the reporting info  */
    for (idx = 0; idx < lengthof(server_side_reporting_info); idx++) {

/* Attempt to update the reporting info */
        esp_err_t err = esp_zb_zcl_update_reporting_info(&server_side_reporting_info[idx]);
        if (err != ESP_OK) {
            ESP_LOGE(ZB_TAG, "Failed to update reporting info for cluster 0x%x: %s", server_side_reporting_info[idx].cluster_id, esp_err_to_name(err));
        } else {
            ESP_LOGI(ZB_TAG, "Successfully updated reporting info for cluster 0x%x.", server_side_reporting_info[idx].cluster_id);
        }
    }
}

static esp_err_t zb_attribute_handler(const esp_zb_zcl_set_attr_value_message_t *message)
{
    esp_err_t ret = ESP_OK;

    ESP_RETURN_ON_FALSE(message, ESP_FAIL, ZB_TAG, "Empty message");
    ESP_RETURN_ON_FALSE(message->info.status == ESP_ZB_ZCL_STATUS_SUCCESS, ESP_ERR_INVALID_ARG, ZB_TAG, "Received message: error status(%d)",
                        message->info.status);
    unsigned val = 0;
    memcpy(&val, message->attribute.data.value, message->attribute.data.size < sizeof(val) ? message->attribute.data.size : sizeof(val));
    ESP_LOGI(ZB_TAG, "Received message: endpoint(%d), cluster(0x%x), attribute(0x%x), data type(%#x), value(%#x)", message->info.dst_endpoint, message->info.cluster,
             message->attribute.id, message->attribute.data.type, val);
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
void app_main(void)
{
    init_gpio();

    esp_zb_platform_config_t config = {
        .radio_config = ESP_ZB_DEFAULT_RADIO_CONFIG(),
        .host_config = ESP_ZB_DEFAULT_HOST_CONFIG(),
    };
    ESP_ERROR_CHECK(nvs_flash_init());
    ESP_ERROR_CHECK(esp_zb_platform_config(&config));
    init_timer(&timer, timer_resolution);
    nvs_main_task_read_vars();

    xTaskCreate(esp_zb_task, "Zigbee_main", 1024*8, NULL, 2, NULL);

    gpio_set_level(indication_led_pin, 0);

    xMainQueue = xQueueCreateStatic(QUEUE_LENGTH, QUEUE_ITEM_SIZE, ucQueueStorageArea, &xStaticQueue );

    motor_control_task(NULL);
}

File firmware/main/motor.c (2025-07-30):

/*
 * Zigbee Roller Shade Example
 *
 * Unless required by applicable law or agreed to in writing, this
 * software is distributed on an "AS IS" BASIS, WITHOUT WARRANTIES OR
 * CONDITIONS OF ANY KIND, either express or implied.
 * 2025/07
 * License: BSD-2
 */

#include "driver/uart.h"
#include "driver/gptimer.h"
#include "driver/gpio.h"
#include "esp_check.h"
#include "esp_err.h"
#include "esp_log.h"
#include "esp_zigbee_core.h"
#include "esp_system.h"
#include "motor.h"

#define MOTOR_PIN_A 0
#define MOTOR_PIN_B 1

/* Level to be used for stopping the motor: 1 = active braking, 0 = free coasting */
#define PIN_IDLE_LEVEL 1

#if PIN_IDLE_LEVEL
#define ZERO_SPEED_DUTY MOTOR_PWM_DUTY_MAX
#else
#define ZERO_SPEED_DUTY 0
#endif



/* Timer configuration */
static const
ledc_timer_config_t timer_conf = {
    .speed_mode = LEDC_LOW_SPEED_MODE,
    .timer_num = LEDC_TIMER_0,
    .duty_resolution = MOTOR_PWM_RESOLUTION,
    .freq_hz = 24000,
    .clk_cfg = LEDC_AUTO_CLK
};

/* LEDC channel configuration */
static const
ledc_channel_config_t channel_conf = {
    .gpio_num = MOTOR_PIN_A,
    .speed_mode = LEDC_LOW_SPEED_MODE,
    .channel = LEDC_CHANNEL_0,
    .timer_sel = LEDC_TIMER_0,
    .duty = 0,
    .hpoint = 0,
    .flags.output_invert = PIN_IDLE_LEVEL != 0,
};


/* Current direction. */
static int currentDirection = MOTOR_DIRECTION_UP;

static int running = 0;

esp_err_t pwm_motor_init(void)
{
    ESP_RETURN_ON_ERROR(ledc_timer_config(&timer_conf), "pwm_motor", "Timer config failed");

/* Configure PWM output channel (only one pin will use PWM at a time) */
    ESP_RETURN_ON_ERROR(ledc_channel_config(&channel_conf), "pwm_motor", "Channel config failed");

/* Configure pin directions */
    ESP_RETURN_ON_ERROR(gpio_set_direction(MOTOR_PIN_A, GPIO_MODE_OUTPUT), "pwm_motor", "GPIO direction failed");
    ESP_RETURN_ON_ERROR(gpio_set_level(MOTOR_PIN_A, PIN_IDLE_LEVEL), "pwm_motor", "GPIO set level failed");
    ESP_RETURN_ON_ERROR(gpio_set_direction(MOTOR_PIN_B, GPIO_MODE_OUTPUT), "pwm_motor", "GPIO direction failed");
    ESP_RETURN_ON_ERROR(gpio_set_level(MOTOR_PIN_B, PIN_IDLE_LEVEL), "pwm_motor", "GPIO set level failed");
    return ESP_OK;
}


static esp_err_t pwm_motor_fade_to(uint32_t target_duty, int fade_time_ms)
{
    if (fade_time_ms < 150)
        fade_time_ms = 150;

    if (fade_time_ms > 1000)
        fade_time_ms = 1000;

    ESP_RETURN_ON_ERROR(ledc_fade_func_install(0), "pwm_motor", "Fade func install failed");

    ESP_RETURN_ON_ERROR(ledc_set_fade_with_time(LEDC_LOW_SPEED_MODE, LEDC_CHANNEL_0, target_duty, fade_time_ms), "pwm_motor", "Set fade with time failed");

    ESP_RETURN_ON_ERROR(ledc_fade_start(LEDC_LOW_SPEED_MODE, LEDC_CHANNEL_0, LEDC_FADE_WAIT_DONE), "pwm_motor", "Set fade start failed");

    ledc_fade_func_uninstall();

    return ESP_OK;
}

esp_err_t pwm_motor_stop(void)
{
    esp_err_t res = ledc_stop(LEDC_LOW_SPEED_MODE, LEDC_CHANNEL_0, PIN_IDLE_LEVEL);

    uint32_t duty = ledc_get_duty(LEDC_LOW_SPEED_MODE, LEDC_CHANNEL_0);

    if (PIN_IDLE_LEVEL)
        duty = MOTOR_PWM_DUTY_MAX - duty;

    pwm_motor_fade_to(ZERO_SPEED_DUTY, duty * 4);

/* Delay to make sure the motor has stopped when this function returns */
    vTaskDelay((duty * 4 + 50) / portTICK_PERIOD_MS);

    running = 0;
    return res;
}

esp_err_t pwm_motor_run(int direction, unsigned int speed)
{
    if (0 == speed) {
        return pwm_motor_stop();
    }

    unsigned int duty = speed;
/* Invert PWM duty setting if idle level is 1. Future IDF versions may fix this. */
    if (PIN_IDLE_LEVEL)
        duty = MOTOR_PWM_DUTY_MAX - duty;

    if (duty > MOTOR_PWM_DUTY_MAX) duty = MOTOR_PWM_DUTY_MAX;

/* If changing direction, first stop the motor */
    if (currentDirection == !direction) {
        ESP_RETURN_ON_ERROR(pwm_motor_stop(), "pwm_motor", "Stopping failed");
    }

    int pwm_pin, high_pin;
    if (MOTOR_DIRECTION_UP == !!direction) { // Upwards: pinB = 1, pinA = PWM
        pwm_pin = MOTOR_PIN_A;
        high_pin = MOTOR_PIN_B;
    } else { // Reverse: pinA = 1, pinB = PWM
        pwm_pin = MOTOR_PIN_B;
        high_pin = MOTOR_PIN_A;
    }



/* Select the appropriate pin for PWM output */
    ESP_RETURN_ON_ERROR(ledc_set_pin(pwm_pin, LEDC_LOW_SPEED_MODE, LEDC_CHANNEL_0), "pwm_motor", "Set PWM pin failed");

/* Set the other pin to idle level */
    ESP_RETURN_ON_ERROR(gpio_set_direction(high_pin, GPIO_MODE_OUTPUT), "pwm_motor", "GPIO direction failed");
    ESP_RETURN_ON_ERROR(gpio_set_level(high_pin, PIN_IDLE_LEVEL), "pwm_motor", "Set idle pin failed");

/* Activate the channel */
#if 0
    ESP_RETURN_ON_ERROR(ledc_set_duty(LEDC_LOW_SPEED_MODE, LEDC_CHANNEL_0, duty), "pwm_motor", "Set duty failed");
    ESP_RETURN_ON_ERROR(ledc_update_duty(LEDC_LOW_SPEED_MODE, LEDC_CHANNEL_0), "pwm_motor", "Update duty failed");
    vTaskDelay(100 / portTICK_PERIOD_MS);
#else
/* Set duty to zero speed to avoid jerking start */
    ESP_RETURN_ON_ERROR(ledc_set_duty(LEDC_LOW_SPEED_MODE, LEDC_CHANNEL_0, ZERO_SPEED_DUTY), "pwm_motor", "Set duty failed");
    ESP_RETURN_ON_ERROR(ledc_update_duty(LEDC_LOW_SPEED_MODE, LEDC_CHANNEL_0), "pwm_motor", "Update duty failed");
/* Fade into target duty with constant acceleration (4 duty steps/ms) */
    pwm_motor_fade_to(duty, speed * 4);
#endif
    ESP_LOGI("Motor", "Motor is running. Speed %u, direction: %d", speed, direction);

    currentDirection = !!direction;
    running = 1;
    return ESP_OK;
}

bool pwm_motor_running(void)
{
    return running != 0;
}

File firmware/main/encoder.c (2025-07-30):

/*
 * Quad encoder support functions (via Pulse Counter module)
 *
 * Unless required by applicable law or agreed to in writing, this
 * software is distributed on an "AS IS" BASIS, WITHOUT WARRANTIES OR
 * CONDITIONS OF ANY KIND, either express or implied.
 * 2025/07
 * License: BSD-2
 */

#include "driver/gpio.h"
#include "esp_check.h"
#include "esp_err.h"
#include "esp_log.h"
#include "esp_zigbee_core.h"
#include "clock.h"
#include "encoder.h"

#define ENCODER_PIN_PWR 12
#define ENCODER_PIN_A   11
#define ENCODER_PIN_B   10

#define ENCODER_4COUNTS_PER_PULSE 0

#define POWER_ACTIVE_LEVEL 1
#define INVALID_WATCH_POINT ((int)-1)

static const char *TAG = "pcnt";

static const
pcnt_unit_config_t unitConfig = {
    .high_limit = 10000,
    .low_limit = -10000,
    .flags = {
        .accum_count = true,
    },
};

static const
pcnt_glitch_filter_config_t filterConfig = {
    .max_glitch_ns = 10000,
};

static const
pcnt_chan_config_t chanConfigA = {
    .edge_gpio_num = ENCODER_PIN_A,
    .level_gpio_num = ENCODER_PIN_B,
};

static const
pcnt_chan_config_t chanConfigB = {
    .edge_gpio_num = ENCODER_PIN_B,
    .level_gpio_num = ENCODER_PIN_A,
};


/****
*   Pulse counter can not be set to an arbitrary value at startup.
*   It can only be reset to 0.
*   Therefore, we need to save the current encoder position to the NVM.
*   After reboot this position becomes the offset to be added to the value of the counter.
*   This way we can keep track of the motor position between power cycles.
*   This module does not have access to the NVM.
*   Calling side must use set_encoder_position() to set the correct offset.
****/
static int32_t startupOffset = 0;

static int32_t accumulator = 0;
static int32_t previous = 0;

static pcnt_unit_handle_t pcntUnit;
static pcnt_channel_handle_t pcntChannelA;
static pcnt_channel_handle_t pcntChannelB;

esp_err_t rotary_encoder_init(void)
{
    ESP_LOGI(TAG, "install pcnt unit");
    ESP_RETURN_ON_ERROR(pcnt_new_unit(&unitConfig, &pcntUnit), TAG, "PCNT new unit failed");

    ESP_LOGI(TAG, "set glitch filter");
    ESP_RETURN_ON_ERROR(pcnt_unit_set_glitch_filter(pcntUnit, &filterConfig), TAG, "PCNT glitch filter failed");

    ESP_LOGI(TAG, "install pcnt channels");
    ESP_RETURN_ON_ERROR(pcnt_new_channel(pcntUnit, &chanConfigA, &pcntChannelA), TAG, "PCNT channel A failed");
    ESP_RETURN_ON_ERROR(pcnt_new_channel(pcntUnit, &chanConfigB, &pcntChannelB), TAG, "PCNT channel B failed");

    ESP_LOGI(TAG, "set edge and level actions for pcnt channels %u", sizeof(int));

#if ENCODER_4COUNTS_PER_PULSE
    ESP_RETURN_ON_ERROR(pcnt_channel_set_edge_action(pcntChannelA, PCNT_CHANNEL_EDGE_ACTION_DECREASE, PCNT_CHANNEL_EDGE_ACTION_INCREASE), TAG, "PCNT edge action failed");
    ESP_RETURN_ON_ERROR(pcnt_channel_set_level_action(pcntChannelA, PCNT_CHANNEL_LEVEL_ACTION_KEEP, PCNT_CHANNEL_LEVEL_ACTION_INVERSE), TAG, "PCNT level action failed");
    ESP_RETURN_ON_ERROR(pcnt_channel_set_edge_action(pcntChannelB, PCNT_CHANNEL_EDGE_ACTION_INCREASE, PCNT_CHANNEL_EDGE_ACTION_DECREASE), TAG, "PCNT edge action failed");
    ESP_RETURN_ON_ERROR(pcnt_channel_set_level_action(pcntChannelB, PCNT_CHANNEL_LEVEL_ACTION_KEEP, PCNT_CHANNEL_LEVEL_ACTION_INVERSE), TAG, "PCNT level action failed");
#else /* 1 count per pulse */
    ESP_RETURN_ON_ERROR(pcnt_channel_set_edge_action(pcntChannelA, PCNT_CHANNEL_EDGE_ACTION_DECREASE, PCNT_CHANNEL_EDGE_ACTION_HOLD), TAG, "PCNT edge action failed");
    ESP_RETURN_ON_ERROR(pcnt_channel_set_level_action(pcntChannelA, PCNT_CHANNEL_LEVEL_ACTION_KEEP, PCNT_CHANNEL_LEVEL_ACTION_INVERSE), TAG, "PCNT level action failed");
    ESP_RETURN_ON_ERROR(pcnt_channel_set_edge_action(pcntChannelB, PCNT_CHANNEL_EDGE_ACTION_HOLD, PCNT_CHANNEL_EDGE_ACTION_HOLD), TAG, "PCNT edge action failed");
    ESP_RETURN_ON_ERROR(pcnt_channel_set_level_action(pcntChannelB, PCNT_CHANNEL_LEVEL_ACTION_KEEP, PCNT_CHANNEL_LEVEL_ACTION_INVERSE), TAG, "PCNT level action failed");
#endif

    ESP_RETURN_ON_ERROR(gpio_set_direction(ENCODER_PIN_PWR, GPIO_MODE_OUTPUT), TAG, "GPIO direction failed");
    ESP_RETURN_ON_ERROR(gpio_set_level(ENCODER_PIN_PWR, !POWER_ACTIVE_LEVEL), TAG, "GPIO set level failed");

    ESP_RETURN_ON_ERROR(pcnt_unit_enable(pcntUnit), TAG, "PCNT unit enable failed");
    ESP_RETURN_ON_ERROR(pcnt_unit_clear_count(pcntUnit), TAG, "PCNT clear count failed");
    return ESP_OK;
}

esp_err_t get_encoder_position(int32_t *pos)
{
    int value = 0;
    ESP_RETURN_ON_ERROR(pcnt_unit_get_count(pcntUnit, &value), TAG, "Reading counter failed (get)");
    if ((value >= 0) && (previous - value > unitConfig.high_limit / 2)) {
        accumulator += unitConfig.high_limit;
    }

    if ((value <= 0) && (previous - value < unitConfig.low_limit / 2)) {
        accumulator += unitConfig.low_limit;
    }

    previous = value;
    *pos = accumulator + value - startupOffset;
    return ESP_OK;
}
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

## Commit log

2025-07-03 Initial upload.
    [motor-esp32h2.kicad_pcb, motor-esp32h2.kicad_sch, partitions.csv]
2025-07-08 Move source files to a separate folder for cleaner directory structure.
    [partitions.csv]
2025-07-29 Remove factory partition, increase size of the OTA partitions.
    [partitions.csv]
2025-07-29 Change firmware version to prevent accidental update of the old boards with different encoder connection.
2025-07-29 Correct the typo that throws compilation error.
    [main.c]
2025-07-29 Track project dependencies
2025-07-31 Add extra checks to up/down commands to avoid possible small moves in a wrong direction.
    [main.c]
